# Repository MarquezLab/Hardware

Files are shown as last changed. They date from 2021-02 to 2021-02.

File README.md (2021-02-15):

# Hardware for implementing behavioural experiments using pyControl 
# (Custom-made pellet dispenser and food-receptacle)

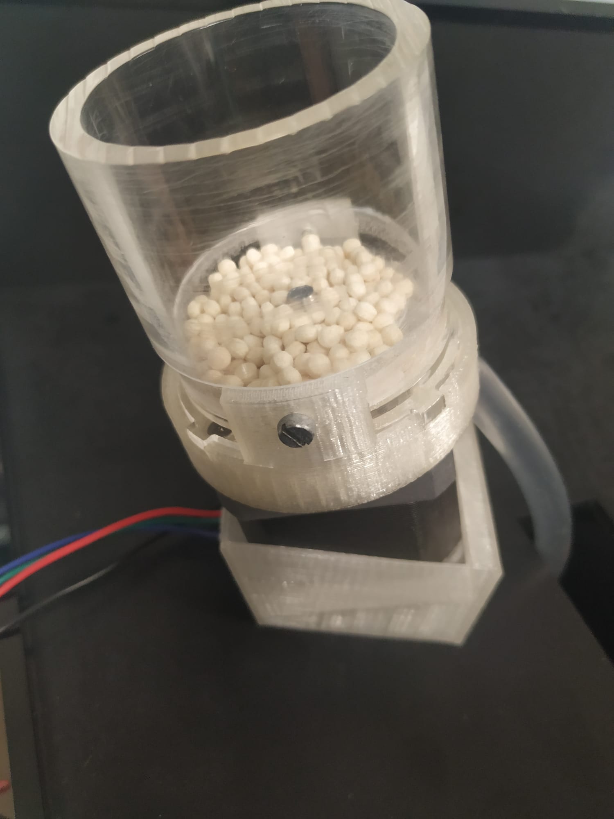
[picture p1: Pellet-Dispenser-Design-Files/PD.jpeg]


The folder contains design files of a custom-made pellet dispenser for delivering 20mg Dustless Precission Pellets (Bio-Serv) in behavioural experiments with mice. Built on a NEMA-17 stepper motor.
The folder contains .stl files for 3D printing of different components. As well as some .pdf files used to laser-cut some acrylic components. It contains a [.pdf file](https://github.com/MarquezLab/Hardware/blob/main/Pellet-Dispenser-Design-Files/MOUNTING%20pellet%20dispenser.pdf) with the setps to follow in order to mount the pellet dispenser. 

There are some extra .stl files. One of the food-magazine used to hold the delivered pellets from where mice can grab them. The design is compatible with a pyControl poke device to detect pellet arrival and retrieval. And another one which was used to hold 2 pellet dispensers together in a wall.

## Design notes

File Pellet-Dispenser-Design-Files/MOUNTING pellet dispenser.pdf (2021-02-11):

PELLET DISPENSER.

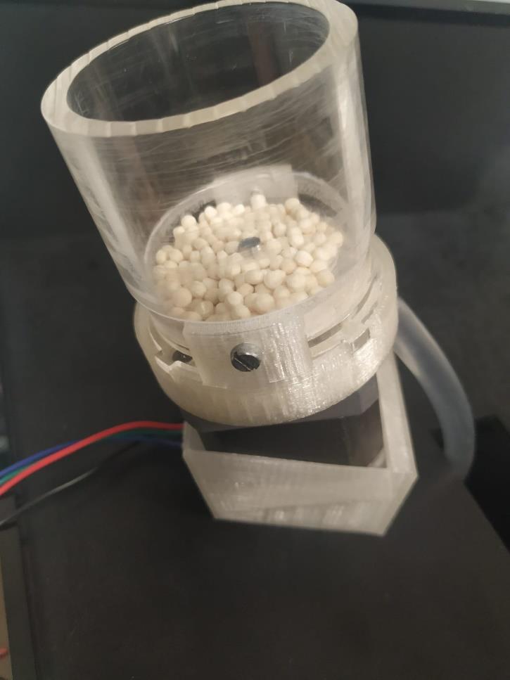
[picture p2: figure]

This pellet dispenser was used with 20 mg Dustless Precision Pellets® Rodent (Bio-Serv).

The reference of the nema 17 stepper motors used is: H2HB34F08AB. Importantly it has a

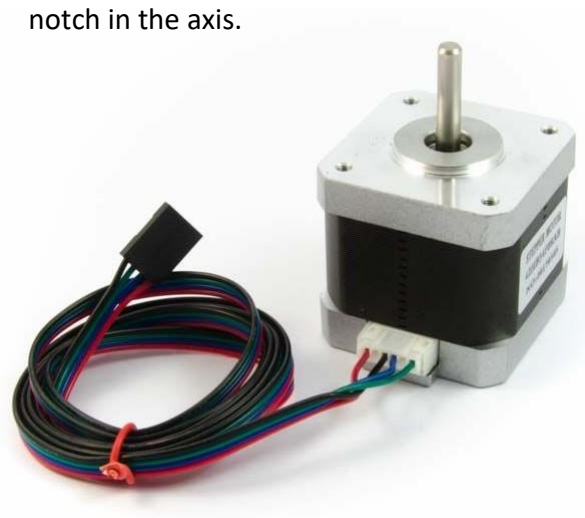
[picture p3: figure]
notch in the axis.
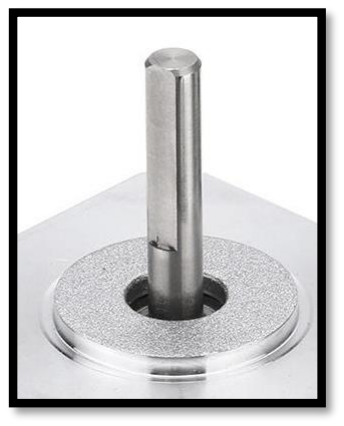
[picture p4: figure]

In order to mount it, you will need two 3mm screws and one no-cap 2mm screw, as well as 2mm and 3mm taps for threading.

There are some 3D printed pieces and some laser-cut acrylic pieces. The acrylic pieces are used to smooth the friction between the pellets and the parts, friction that slowly destroys the pellets and forms dust that eventually might stop the pellet-dispenser well-functioning.

(A) Holes to screw pellets holder cylinder (https://github.com/MarquezLab/Hardware/blob/main/Pellet-Dispenser-Design-Files/Pellets%20holder%20cilinder.stl)

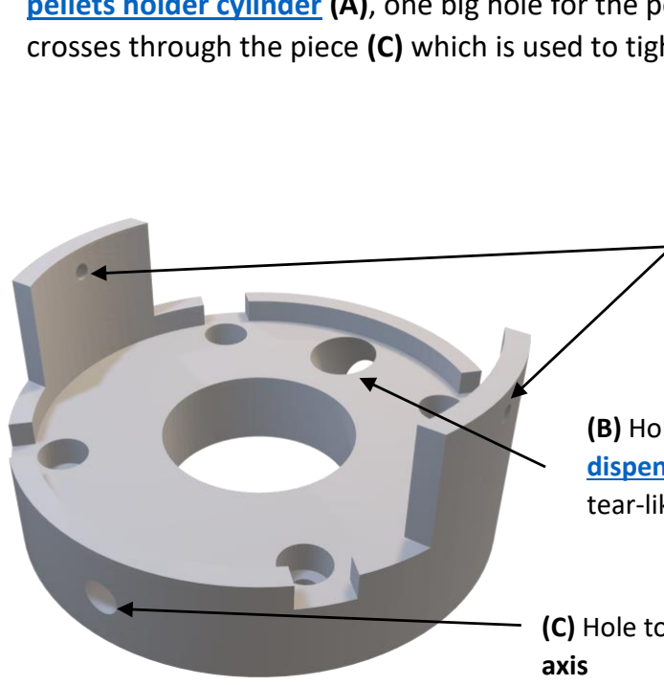
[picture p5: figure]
axis

(B) Hole for dropping pellet. Should be aligned with the pellet dispenser base top (https://github.com/MarquezLab/Hardware/blob/main/Pellet-Dispenser-Design-Files/pellet%20dispenser%20base%20top%20acrylic%20-3mm.pdf) hole and with the pellets holder cylinder (https://github.com/MarquezLab/Hardware/blob/main/Pellet-Dispenser-Design-Files/Pellets%20holder%20cilinder.stl) tear-like piece.
(C) Hole to tight the wheel (https://github.com/MarquezLab/Hardware/blob/main/Pellet-Dispenser-Design-Files/wheel%20-%202mm.pdf) holder piece to the motor

## MOUNTING STEPS:

Unscrew the motor stepper motor screws from the bottom part.

Put pellet dispenser base (https://github.com/MarquezLab/Hardware/blob/main/Pellet-Dispenser-Design-Files/Pellet%20dispenser%20base.stl) 3D piece on top of the motor and screw it with the 4 screws that were removed previously. Notice that this piece has different holes. 2 holes to screw the pellets holder cylinder (https://github.com/MarquezLab/Hardware/blob/main/Pellet-Dispenser-Design-Files/Pellets%20holder%20cilinder.stl) (A), one big hole for the pellet to fall (B) and another hole that crosses through the piece (C) which is used to tight the wheel to the axis of the motor.

Put the 3mm acrylic pellet dispenser base top (https://github.com/MarquezLab/Hardware/blob/main/Pellet-Dispenser-Design-Files/pellet%20dispenser%20base%20top%20acrylic%20-3mm.pdf) piece on top of the pellet dispenser base (https://github.com/MarquezLab/Hardware/blob/main/Pellet-Dispenser-Design-Files/Pellet%20dispenser%20base.stl) , fitting the notches.

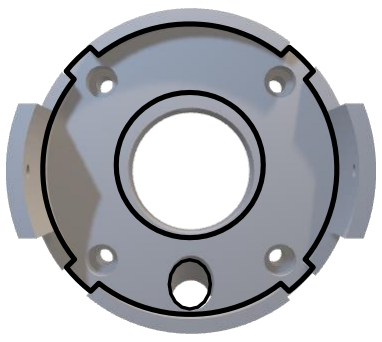
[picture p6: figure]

Glue the 2mm acrylic wheel (https://github.com/MarquezLab/Hardware/blob/main/Pellet-Dispenser-Design-Files/wheel%20-%202mm.pdf) piece with the wheel-motoraxis holder (https://github.com/MarquezLab/Hardware/blob/main/Pellet-Dispenser-Design-Files/wheel-motoraxis%20holder.stl) piece, keeping the notch aligned of both pieces.

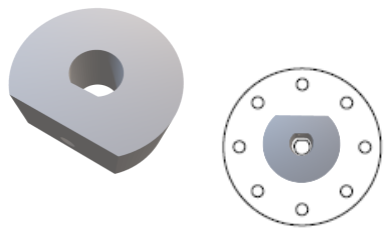
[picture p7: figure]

2mm acrylic wheel

1mm space

1mm space

Once glued, put the wheel with the part of the wheel-motoraxis holder (https://github.com/MarquezLab/Hardware/blob/main/Pellet-Dispenser-Design-Files/wheel-motoraxis%20holder.stl) facing bottom towards the motor and the wheel facing up, through the motor axis, which has a notch same as this piece. The little hole on the pellet dispenser base can be used to tight the wheel to the axis with a non-cap 2mm screw.

Importantly, the wheel (https://github.com/MarquezLab/Hardware/blob/main/Pellet-Dispenser-Design-Files/wheel%20-%202mm.pdf) piece should have of about 1 mm,
between the acrylic on the top of the pellet dispenser base and the cylinder to let the wheel rotate freely with
no friction on the top or bottom and also to let the dust, that sometimes is created, to go out from the pellet dispenser to allow a correct functioning.

Screw the pellets holder cylinder (https://github.com/MarquezLab/Hardware/blob/main/Pellet-Dispenser-Design-Files/Pellets%20holder%20cilinder.stl) to the pellet dispenser base (https://github.com/MarquezLab/Hardware/blob/main/Pellet-Dispenser-Design-Files/Pellet%20dispenser%20base.stl) with two 3mm screws (1). Keep the little tear-like piece of the pellets holder cylinder facing on top of the big hole of the pellet dispenser base (2).

(1) (2)

Note that, the pellets holder cylinder (https://github.com/MarquezLab/Hardware/blob/main/Pellet-Dispenser-Design-Files/Pellets%20holder%20cilinder.stl) is 3D printed, but I used 5cm diameter transparent acrylic cylinder, which allows to see the pellets and is useful to check if they get stuck.

Finally, put a silicon tube (0.8cm diameter) of the desired length fitting the hole in the pellet dispenser base (https://github.com/MarquezLab/Hardware/blob/main/Pellet-Dispenser-Design-Files/Pellet%20dispenser%20base.stl) until touching the pellet dispenser base top acrylic (https://github.com/MarquezLab/Hardware/blob/main/Pellet-Dispenser-Design-Files/pellet%20dispenser%20base%20top%20acrylic%20-3mm.pdf) piece from the bottom. You might need to cut the tip of the tube to be flat.

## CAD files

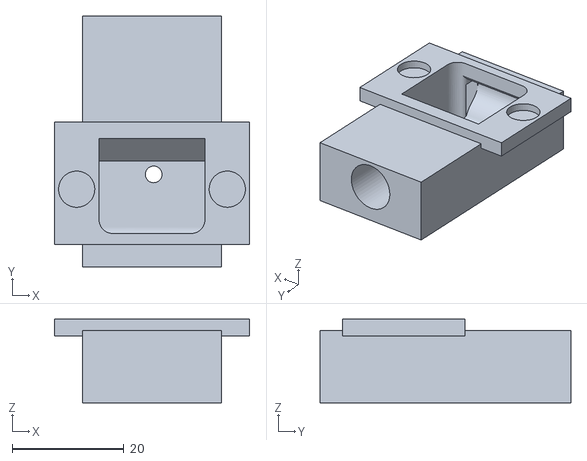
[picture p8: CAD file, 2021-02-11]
Feeder-magnets.stl
35.0 x 45.0 x 15.0

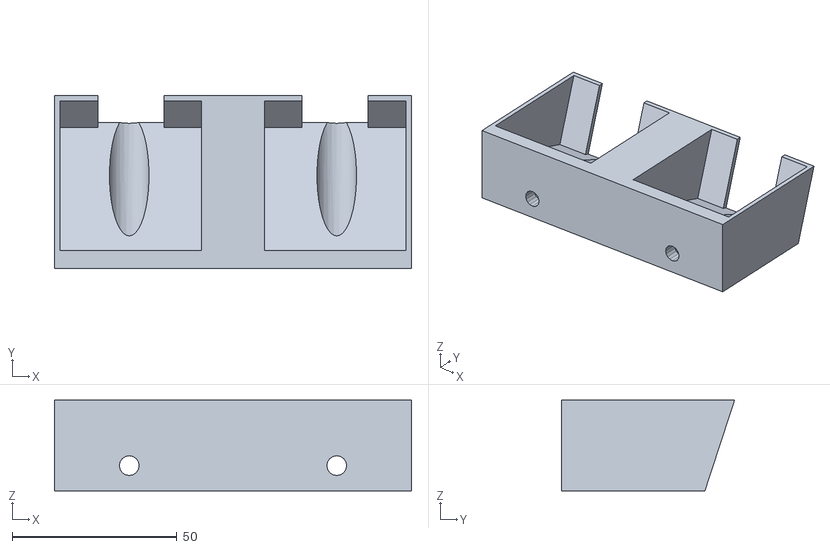
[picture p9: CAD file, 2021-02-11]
Pellet-Dispenser-Design-Files/motor holders.stl
108.2 x 52.5 x 27.5

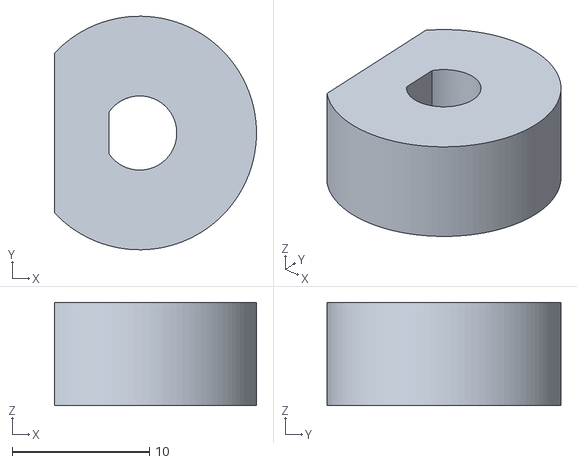
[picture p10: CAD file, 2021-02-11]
Pellet-Dispenser-Design-Files/wheel-motoraxis holder.stl
14.7 x 17.0 x 7.50

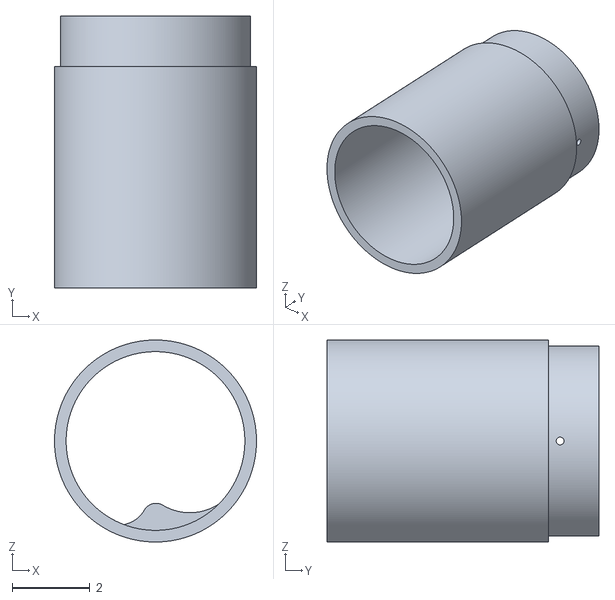
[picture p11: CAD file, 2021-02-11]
Pellet-Dispenser-Design-Files/Pellets holder cilinder.stl
5.20 x 7.00 x 5.20

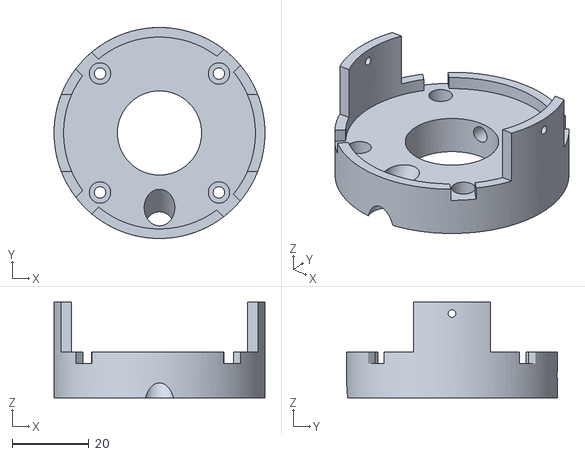
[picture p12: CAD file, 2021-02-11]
Pellet-Dispenser-Design-Files/Pellet dispenser base.stl
55.0 x 55.0 x 25.0
